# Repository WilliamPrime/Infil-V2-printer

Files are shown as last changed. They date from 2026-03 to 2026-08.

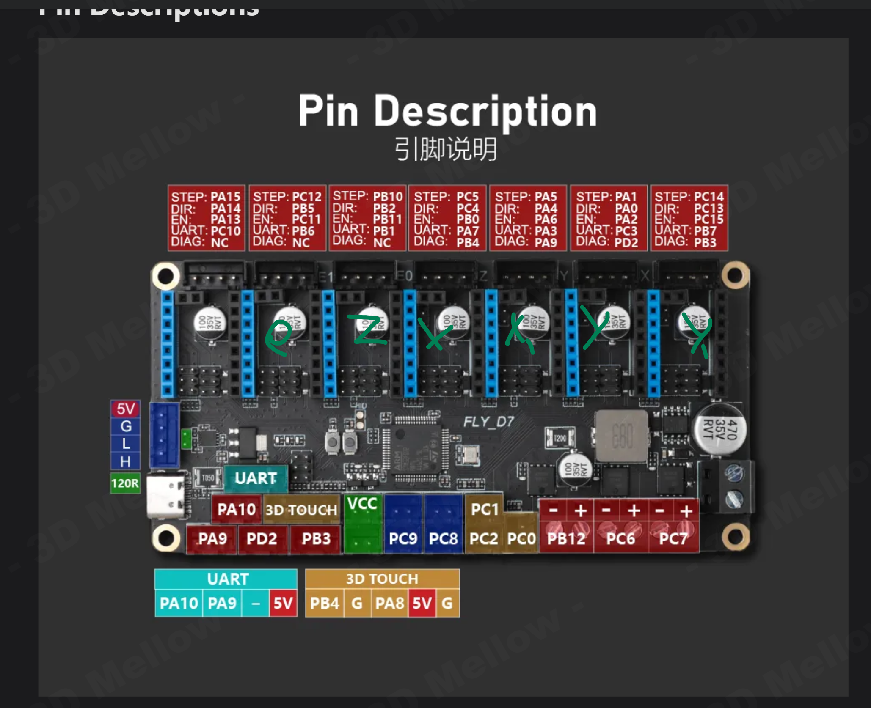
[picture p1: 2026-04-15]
Klipper/Screenshot 2026-04-15 025206.png

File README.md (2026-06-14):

# Breaky Belt

## What is Breaky Belt? 
Breaky belt is a belt printer that prints at an angle, in theory allowing infinetly long prints.

Some of the printers that inspired me to make this are:
- [Baby Belt](https://github.com/RobMink/BabyBeltPro)
- [Annex K3](https://github.com/Annex-Engineering/Gasherbrum-K3)

_DSC5262
_DSC5261
_DSC5266
_DSC5264

## why is it called the Breaky Belt?
Originally it was going to be called the Belty Boi, however, when modeling it in fusion i kept encountering issues, so it got renamed to the breaky belt.
Dont worry though, hopefully it shouldnt break on you!

An alterative name i was considering was BRRRTT, pronounced Bert, it was supposed to mimic the sound the printer makes while printing quickly.

# WARNING BEFORE YOU CONSIDER BUILDING ONE

ALL OF THE FILES IN THE REPO HAVENT BEEN TESTED YET

there are currently some issues ive encountered
1. There is a clearance issue with a couple of gantry parts removing ~10mm of x travel
2. The files have only been tested with MGN9H instead of the intended MGN9C, I accidentally ordered the wrong rails and didnt have time to order new ones
3. Electronics are currently free to roam arround whatever surface the printer is on, its not the best
4. Currently the dual SKR mini config isnt the original inteded cofig, its currently operating at 1.77A @ 24V per motor, as opposed to the 2.5A @ 48V per motor its capable of, this is due to me not being able to figure out the firmware for the board I chose, if you choose something like a btt octopus or a mellow fly super , you shouldnt run into this issue. Reguardless of how you fix it, im not exactly sure of the max capabilities of the printer at the moment, 1300mm/s @ 37K Accel was comfortable acchived without motor tuning or experimentation into rubber band systems to counter the weight of toolhead

# building it
On the topic of it breaking on you (which hopefully it shouldnt do).
When building it, I would suggest you build the bed assembly first.And assemble it as shown in the following animation

https://github.com/user-attachments/assets/72ef6f26-8bf3-4d65-aa56-422cc91b3fcc

When building it you will find the CAD for the extruder is not included
the mounting holes for the extruder support anything with the same mounting as the sherpa mini
for my build im using the [ProtoXtruder 2.0 by Nhchiu](https://github.com/nhchiu/3DPrinter-Designs/tree/main/ProtoXtruder_2.0)

# Parts/BOM

[_Here_](https://github.com/WilliamPrime/Infil-V2-printer/blob/main/BOM.csv) is the BOM

If you allready have some of the parts, [_this_](https://github.com/WilliamPrime/Infil-V2-printer/blob/main/Interactive%20BOM.xlsx) version of the bom lets you remove parts and tick them off

In terms of filament, i recomend using ABS, you will need
~1300g of primary colour
~600g of secondary colour

£

# bonus photo with Orpheus for scale
_DSC5265

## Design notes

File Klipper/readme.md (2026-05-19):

# THESE CONFIGS WORK WITH A PAIR OF SKR MINI E3 V3s 

# MODIFICATIONS ARE NEEDED TO GET THE MELLOW D7 and TMC5160s WORKING TO ENABLE 48V SUPPORT

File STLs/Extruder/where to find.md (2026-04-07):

Due to the liscence of the extruder im not including it in this repo.

My choice was the ProtoXtruder which can be found [here ](https://github.com/nhchiu/3DPrinter-Designs/tree/main/ProtoXtruder_2.0).
Another great choice for a compatible extruder is the [sherpa mini](https://github.com/Annex-Engineering/Sherpa_Mini-Extruder).

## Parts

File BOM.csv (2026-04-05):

 |  | pack size (where aplicable) | Cost | Quant | Total for item | Link | Notes
MOTION
Reinforced Gt2 belt 2M |  |  | 11.58 | 1 | 11.58 | https://www.aliexpress.com/item/1005010353468208.html | printer requires exactly 2.1meters of belt, make sure to buy a little bit more
Toothed 20t idler |  | 4pack | 16.14 | 0 | 0.00 | https://www.aliexpress.com/item/1005002630474461.html
625 bearings |  | 1pk | 0.1186 | 16 | 1.90 | https://jlcmc.com/product/b/C15/BR8364/deep-groove-ball-bearing-double-side-with-dust-cover
5mm couplers |  | 1pk | 1.56 | 4 | 6.24 | https://www.aliexpress.com/item/1005008857891214.html | 5x5 | cheaper than jlc
5mm dia 11mm shaft |  |  | 0.6632 | 4 | 2.66 | https://jlcmc.com/product/s/B08/BACA/linear-shaft-solid-straight-g6-tolerance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
5mm dia 50mm shaft |  |  | 0.75 | 4 | 3.00 | https://jlcmc.com/product/s/B08/BACA/linear-shaft-solid-straight-g6-tolerance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
5mm dia 142mm shaft |  |  | 1.1663 | 2 | 2.34 | https://jlcmc.com/product/s/B08/BACA/linear-shaft-solid-straight-g6-tolerance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
Z1 mgn9c 314mm |  |  | 10.951 | 1 | 10.96 | https://jlcmc.com/product/s/B03/E-BMN/economical-linear-guide-mini-standard-type-7-9-12-15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
Z1 mgn9c 160mm |  |  | 7.3636 | 2 | 14.73 | https://jlcmc.com/product/s/B03/E-BMN/economical-linear-guide-mini-standard-type-7-9-12-15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
Z1 mgn9c 224mm |  |  | 8.8442 | 3 | 26.54 | https://jlcmc.com/product/s/B03/E-BMN/economical-linear-guide-mini-standard-type-7-9-12-15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
LDO2504AH |  | Inc shipping 4pk | 107.87 | 1 | 107.87 | https://www.onetwo3d.co.uk/product/ldo-42sth48-2504ahs35r-stepper-motor/ | CAD uses 30mm shaft motors, these are 35mm shaft motors , spacers required
FRAME
2020 , 180mm |  |  | 0.4712 | 2 | 0.95 | https://jlcmc.com/product/s/T01/TXCJ/extruded-aluminum-t-slot-20-series(eu)?k=TXCJ-H7-2020D-L180
2020 , 280mm |  |  | 0.7272 | 2 | 1.46 | https://jlcmc.com/product/s/T01/TXCJ/extruded-aluminum-t-slot-20-series(eu)?k=TXCJ-H7-2020D-L280
2020 , 380mm |  |  | 0.9814 | 2 | 1.97 | https://jlcmc.com/product/s/T01/TXCJ/extruded-aluminum-t-slot-20-series(eu)?k=TXCJ-H7-2020D-L380
2020 , 320mm |  |  | 0.8285 | 4 | 3.32 | https://jlcmc.com/product/s/T01/TXCJ/extruded-aluminum-t-slot-20-series(eu)?k=TXCJ-H7-2020D-L320
FASTENERS
m5, 7.5mm od heatset |  | 10pk | 2.39 | 1 | 2.39 | https://www.aliexpress.com/item/1005008897571758.html
m3, m3x5x4.2 |  | 250pk | 7.86 | 1 | 7.86 | https://www.aliexpress.com/item/1005006494200941.html | you could order the exact ammount you need, but if you need to reprint a part and need more heatsets, that could become bad
M5x30 | SHCS |  | 0.0255 | 12 | 0.31
M5x20 | SHCS |  | 0.0167 | 14 | 0.24
M5x12 | SHCS |  | 0.0159 | 60 | 0.96
M5 t slot nut |  |  | 0.0099 | 54 | 0.54 | https://jlcmc.com/product/s/T02/TPAA/m3-m4-m5-t-nut-20-series-aluminum-profile-fasteners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
M4x20 | SHCS |  | 0.156 | 14 | 2.19 | https://jlcmc.com/product/s/E02/EDLA/hex-socket-screw-full-partial-thread-standard-type-(din-912-gb-t-70.1)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
M4x10 | SHCS |  | 0.142 | 5 | 0.71 | https://jlcmc.com/product/s/E02/EDLA/hex-socket-screw-full-partial-thread-standard-type-(din-912-gb-t-70.1)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
M4 t slot nut |  |  | 0.0082 | 20 | 0.17 | https://jlcmc.com/product/s/T02/TPAA/m3-m4-m5-t-nut-20-series-aluminum-profile-fasteners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
M3x40 | SHCS |  | 0.0269 | 11 | 0.30 | https://jlcmc.com/product/s/E02/EDLA/hex-socket-screw-full-partial-thread-standard-type-(din-912-gb-t-70.1)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
M3x35 | SHCS |  | 0.0273 | 5 | 0.14 | https://jlcmc.com/product/s/E02/EDLA/hex-socket-screw-full-partial-thread-standard-type-(din-912-gb-t-70.1)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
M3x30 | SHCS |  | 0.0222 | 8 | 0.18 | https://jlcmc.com/product/s/E02/EDLA/hex-socket-screw-full-partial-thread-standard-type-(din-912-gb-t-70.1)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
M3x25 | SHCS |  | 0.0178 | 7 | 0.13 | https://jlcmc.com/product/s/E02/EDLA/hex-socket-screw-full-partial-thread-standard-type-(din-912-gb-t-70.1)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
M3x22 | SHCS |  | 0.0169 | 8 | 0.14 | https://jlcmc.com/product/s/E02/EDLA/hex-socket-screw-full-partial-thread-standard-type-(din-912-gb-t-70.1)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
M3x20 | SHCS |  | 0.0143 | 3 | 0.05 | https://jlcmc.com/product/s/E02/EDLA/hex-socket-screw-full-partial-thread-standard-type-(din-912-gb-t-70.1)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
M3x16 | SHCS |  | 0.0142 | 23 | 0.33 | https://jlcmc.com/product/s/E02/EDLA/hex-socket-screw-full-partial-thread-standard-type-(din-912-gb-t-70.1)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
M3x12 | SHCS |  | 0.128 | 70 | 8.96 | https://jlcmc.com/product/s/E02/EDLA/hex-socket-screw-full-partial-thread-standard-type-(din-912-gb-t-70.1)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
M3x8 | SHCS |  | 0.0113 | 57 | 0.65 | https://jlcmc.com/product/s/E02/EDLA/hex-socket-screw-full-partial-thread-standard-type-(din-912-gb-t-70.1)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
M3x6 | SHCS |  | 0.0127 | 52 | 0.67 | https://jlcmc.com/product/s/E02/EDLA/hex-socket-screw-full-partial-thread-standard-type-(din-912-gb-t-70.1)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
M3 t slot nut |  |  | 0.0136 | 70 | 0.96
ELECTRONICS
custom v0.1 bed heater |  |  | 5.25 | 1 | 5.25 | JLC flexheater service
IEC power inlet |  |  | 2.05 | 1 | 2.05 | https://www.aliexpress.com/item/1005006990146296.html
external mosfet board to support the bed |  |  | 2.51 | 1 | 2.51 | https://www.aliexpress.com/item/1005006614952857.html
external mosfet board to support the bed |  |  | 2.51 | 1 | 2.51 | https://www.aliexpress.com/item/1005006614952857.html
Ptfe wire red |  |  | 5.69 | 1 | 5.69 | https://www.aliexpress.com/item/1005004874514644.html
Ptfe wire blk |  |  | 5.7 | 1 | 5.70 | https://www.aliexpress.com/item/1005004874514644.html
old desktop fans |  |  | 0 |  |  | hunt
meanwell lrs350-24 |  |  | 42.73 | 1 | 42.73 | https://www.aliexpress.com/item/1005004796910794.html
meanwell lrs350-48 |  |  | 44.2 | 1 | 44.20 | https://www.aliexpress.com/item/1005004796910794.html
mellow D7 |  |  | 24.03 | 1 | 24.03 | https://www.aliexpress.com/item/1005006422323624.html | it’s a much cheaper alternative to the BTT octopus or mellow super
TMC2209 | 2pk |  | 7.39 | 1 | 7.39 | https://www.aliexpress.com/item/33028050145.html
TMC5160 | 1pk |  | 21.72 | 4 | 86.88 | https://www.aliexpress.com/item/1005004229433552.html
Toolhead
peopoly lancer long |  |  | 64.99 | 1 | 64.99 | https://peopoly.net/products/magneto-x-lancer-melt-zone?variant=49972216103194 | 120w heater on it, 15 bucks of the prices is shipping
HGX 2.0 gears + hardware |  |  | 13.85 | 1 | 13.85 | https://www.aliexpress.com/item/1005007316630515.html | comes with other hardware needed
4015 fan |  |  | 2.37 | 1 | 2.37 | https://www.aliexpress.com/item/1005004832141450.html | for low speed PLA
2510 fan |  |  | 1.62 | 1 | 1.62 | https://www.aliexpress.com/item/1005003595630530.html | fan
LDO 36STH20-1004AHG |  |  | 24.11 | 1 | 24.11 | https://www.aliexpress.com/item/1005002899860754.html | Allready own, using from infil v1
OTHER
voron 0 bed |  |  | 13.73 | 1 | 13.73 | https://www.aliexpress.com/item/1005007347759654.html
bed springs |  |  | 1.09 | 1 | 1.09 | https://www.aliexpress.com/item/33000218395.html
gt2 6mm closed loop belt for belt |  |  | 1.94 | 1 | 0.00 | https://www.aliexpress.com/item/1005004019523225.html | 2gt 306 | I allready own this
motor heat sync |  |  | 3.03 | 1 | 3.03 | https://www.aliexpress.com/item/4000723868050.html
SHIPPING
If using JLC the (shipping + taxes + customs) are here, this assumes you used JLC every time I used it |  |  | 90.94 | 1 | 90.94
 |  |  |  |  | Total cost
 |  |  |  |  | 668.07

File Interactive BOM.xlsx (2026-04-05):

 |  | Total cost
 |  | 577.13
Owned? |  |  | pack size (where aplicable) | Cost | Quant | Total From scratch | Total with my parts | Link | Notes
 | MOTION
FALSE | Reinforced Gt2 belt 2M |  |  | 11.58 | 1 | 11.58 | 11.58 | https://www.aliexpress.com/item/1005010353468208.html | printer requires exactly 2.1meters of belt, make sure to buy a little bit more
FALSE | Toothed 20t idler |  | 4pack | 16.14 | 0 | 0.00 | 0 | https://www.aliexpress.com/item/1005002630474461.html
FALSE | 625 bearings |  | 1pk | 0.1186 | 16 | 1.90 | 1.9 | https://jlcmc.com/product/b/C15/BR8364/deep-groove-ball-bearing-double-side-with-dust-cover
FALSE | 5mm couplers |  | 1pk | 1.56 | 4 | 6.24 | 6.24 | https://www.aliexpress.com/item/1005008857891214.html | 5x5 | cheaper than jlc
FALSE | 5mm dia 11mm shaft |  |  | 0.6632 | 4 | 2.66 | 2.66 | https://jlcmc.com/product/s/B08/BACA/linear-shaft-solid-straight-g6-tolerance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
FALSE | 5mm dia 50mm shaft |  |  | 0.75 | 4 | 3.00 | 3 | https://jlcmc.com/product/s/B08/BACA/linear-shaft-solid-straight-g6-tolerance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
FALSE | 5mm dia 142mm shaft |  |  | 1.1663 | 2 | 2.34 | 2.34 | https://jlcmc.com/product/s/B08/BACA/linear-shaft-solid-straight-g6-tolerance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
FALSE | Z1 mgn9c 314mm |  |  | 10.951 | 1 | 10.96 | 10.96 | https://jlcmc.com/product/s/B03/E-BMN/economical-linear-guide-mini-standard-type-7-9-12-15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
FALSE | Z1 mgn9c 160mm |  |  | 7.3636 | 2 | 14.73 | 14.73 | https://jlcmc.com/product/s/B03/E-BMN/economical-linear-guide-mini-standard-type-7-9-12-15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
FALSE | Z1 mgn9c 224mm |  |  | 8.8442 | 3 | 26.54 | 26.54 | https://jlcmc.com/product/s/B03/E-BMN/economical-linear-guide-mini-standard-type-7-9-12-15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
FALSE | LDO2504AH |  | Inc shipping 4pk | 107.87 | 1 | 107.87 | 107.87 | https://www.onetwo3d.co.uk/product/ldo-42sth48-2504ahs35r-stepper-motor/ | CAD uses 30mm shaft motors, these are 35mm shaft motors , spacers required
 | FRAME
FALSE | 2020 , 180mm |  |  | 0.4712 | 2 | 0.95 | 0.95 | https://jlcmc.com/product/s/T01/TXCJ/extruded-aluminum-t-slot-20-series(eu)?k=TXCJ-H7-2020D-L180
FALSE | 2020 , 280mm |  |  | 0.7272 | 2 | 1.46 | 1.46 | https://jlcmc.com/product/s/T01/TXCJ/extruded-aluminum-t-slot-20-series(eu)?k=TXCJ-H7-2020D-L280
FALSE | 2020 , 380mm |  |  | 0.9814 | 2 | 1.97 | 1.97 | https://jlcmc.com/product/s/T01/TXCJ/extruded-aluminum-t-slot-20-series(eu)?k=TXCJ-H7-2020D-L380
FALSE | 2020 , 320mm |  |  | 0.8285 | 4 | 3.32 | 3.32 | https://jlcmc.com/product/s/T01/TXCJ/extruded-aluminum-t-slot-20-series(eu)?k=TXCJ-H7-2020D-L320
 | FASTENERS
FALSE | m5, 7.5mm od heatset |  | 10pk | 2.39 | 1 | 2.39 | 2.39 | https://www.aliexpress.com/item/1005008897571758.html
FALSE | m3, m3x5x4.2 |  | 250pk | 7.86 | 1 | 7.86 | 7.86 | https://www.aliexpress.com/item/1005006494200941.html | you could order the exact ammount you need, but if you need to reprint a part and need more heatsets, that could become bad
FALSE | M5x30 | SHCS |  | 0.0255 | 12 | 0.31 | 0.31
FALSE | M5x20 | SHCS |  | 0.0167 | 14 | 0.24 | 0.24
FALSE | M5x12 | SHCS |  | 0.0159 | 60 | 0.96 | 0.96
FALSE | M5 t slot nut |  |  | 0.0099 | 54 | 0.54 | 0.54 | https://jlcmc.com/product/s/T02/TPAA/m3-m4-m5-t-nut-20-series-aluminum-profile-fasteners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
FALSE | M4x20 | SHCS |  | 0.156 | 14 | 2.19 | 2.19 | https://jlcmc.com/product/s/E02/EDLA/hex-socket-screw-full-partial-thread-standard-type-(din-912-gb-t-70.1)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
FALSE | M4x10 | SHCS |  | 0.142 | 5 | 0.71 | 0.71 | https://jlcmc.com/product/s/E02/EDLA/hex-socket-screw-full-partial-thread-standard-type-(din-912-gb-t-70.1)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
FALSE | M4 t slot nut |  |  | 0.0082 | 20 | 0.17 | 0.17 | https://jlcmc.com/product/s/T02/TPAA/m3-m4-m5-t-nut-20-series-aluminum-profile-fasteners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
FALSE | M3x40 | SHCS |  | 0.0269 | 11 | 0.30 | 0.3 | https://jlcmc.com/product/s/E02/EDLA/hex-socket-screw-full-partial-thread-standard-type-(din-912-gb-t-70.1)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
FALSE | M3x35 | SHCS |  | 0.0273 | 5 | 0.14 | 0.14 | https://jlcmc.com/product/s/E02/EDLA/hex-socket-screw-full-partial-thread-standard-type-(din-912-gb-t-70.1)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
FALSE | M3x30 | SHCS |  | 0.0222 | 8 | 0.18 | 0.18 | https://jlcmc.com/product/s/E02/EDLA/hex-socket-screw-full-partial-thread-standard-type-(din-912-gb-t-70.1)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
FALSE | M3x25 | SHCS |  | 0.0178 | 7 | 0.13 | 0.13 | https://jlcmc.com/product/s/E02/EDLA/hex-socket-screw-full-partial-thread-standard-type-(din-912-gb-t-70.1)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
FALSE | M3x22 | SHCS |  | 0.0169 | 8 | 0.14 | 0.14 | https://jlcmc.com/product/s/E02/EDLA/hex-socket-screw-full-partial-thread-standard-type-(din-912-gb-t-70.1)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
FALSE | M3x20 | SHCS |  | 0.0143 | 3 | 0.05 | 0.05 | https://jlcmc.com/product/s/E02/EDLA/hex-socket-screw-full-partial-thread-standard-type-(din-912-gb-t-70.1)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
FALSE | M3x16 | SHCS |  | 0.0142 | 23 | 0.33 | 0.33 | https://jlcmc.com/product/s/E02/EDLA/hex-socket-screw-full-partial-thread-standard-type-(din-912-gb-t-70.1)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
FALSE | M3x12 | SHCS |  | 0.128 | 70 | 8.96 | 8.96 | https://jlcmc.com/product/s/E02/EDLA/hex-socket-screw-full-partial-thread-standard-type-(din-912-gb-t-70.1)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
FALSE | M3x8 | SHCS |  | 0.0113 | 57 | 0.65 | 0.65 | https://jlcmc.com/product/s/E02/EDLA/hex-socket-screw-full-partial-thread-standard-type-(din-912-gb-t-70.1)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
FALSE | M3x6 | SHCS |  | 0.0127 | 52 | 0.67 | 0.67 | https://jlcmc.com/product/s/E02/EDLA/hex-socket-screw-full-partial-thread-standard-type-(din-912-gb-t-70.1)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
FALSE | M3 t slot nut |  |  | 0.0136 | 70 | 0.96 | 0.96
 |  |  |  |  |  |  | 0
 | ELECTRONICS
FALSE | custom v0.1 bed heater |  |  | 5.25 | 1 | 5.25 | 5.25 | JLC flexheater service
FALSE | IEC power inlet |  |  | 2.05 | 1 | 2.05 | 2.05 | https://www.aliexpress.com/item/1005006990146296.html
FALSE | external mosfet board to support the bed |  |  | 2.51 | 1 | 2.51 | 2.51 | https://www.aliexpress.com/item/1005006614952857.html
FALSE | external mosfet board to support the bed |  |  | 2.51 | 1 | 2.51 | 2.51 | https://www.aliexpress.com/item/1005006614952857.html
FALSE | Ptfe wire red |  |  | 5.69 | 1 | 5.69 | 5.69 | https://www.aliexpress.com/item/1005004874514644.html
FALSE | Ptfe wire blk |  |  | 5.7 | 1 | 5.70 | 5.7 | https://www.aliexpress.com/item/1005004874514644.html
FALSE | old desktop fans |  |  | 0 |  |  | 0 | hunt
FALSE | meanwell lrs350-24 |  |  | 42.73 | 1 | 42.73 | 42.73 | https://www.aliexpress.com/item/1005004796910794.html
FALSE | meanwell lrs350-48 |  |  | 44.2 | 1 | 44.20 | 44.2 | https://www.aliexpress.com/item/1005004796910794.html
FALSE | mellow D7 |  |  | 24.03 | 1 | 24.03 | 24.03 | https://www.aliexpress.com/item/1005006422323624.html | it’s a much cheaper alternative to the BTT octopus or mellow super
FALSE | TMC2209 | 2pk |  | 7.39 | 1 | 7.39 | 7.39 | https://www.aliexpress.com/item/33028050145.html
FALSE | TMC5160 | 1pk |  | 21.72 | 4 | 86.88 | 86.88 | https://www.aliexpress.com/item/1005004229433552.html
 | Toolhead
FALSE | peopoly lancer long |  |  | 64.99 | 1 | 64.99 | 64.99 | https://peopoly.net/products/magneto-x-lancer-melt-zone?variant=49972216103194 | 120w heater on it, 15 bucks of the prices is shipping
FALSE | HGX 2.0 gears + hardware |  |  | 13.85 | 1 | 13.85 | 13.85 | https://www.aliexpress.com/item/1005007316630515.html | comes with other hardware needed
FALSE | 4015 fan |  |  | 2.37 | 1 | 2.37 | 2.37 | https://www.aliexpress.com/item/1005004832141450.html | for low speed PLA
FALSE | 2510 fan |  |  | 1.62 | 1 | 1.62 | 1.62 | https://www.aliexpress.com/item/1005003595630530.html | fan
FALSE | LDO 36STH20-1004AHG |  |  | 24.11 | 1 | 24.11 | 24.11 | https://www.aliexpress.com/item/1005002899860754.html | Allready own, using from infil v1
 | OTHER
FALSE | voron 0 bed |  |  | 13.73 | 1 | 13.73 | 13.73 | https://www.aliexpress.com/item/1005007347759654.html
FALSE | bed springs |  |  | 1.09 | 1 | 1.09 | 1.09 | https://www.aliexpress.com/item/33000218395.html
FALSE | gt2 6mm closed loop belt for belt |  |  | 1.94 | 1 | 0.00 | 0 | https://www.aliexpress.com/item/1005004019523225.html | 2gt 306 | I allready own this
FALSE | motor heat sync |  |  | 3.03 | 1 | 3.03 | 3.03 | https://www.aliexpress.com/item/4000723868050.html

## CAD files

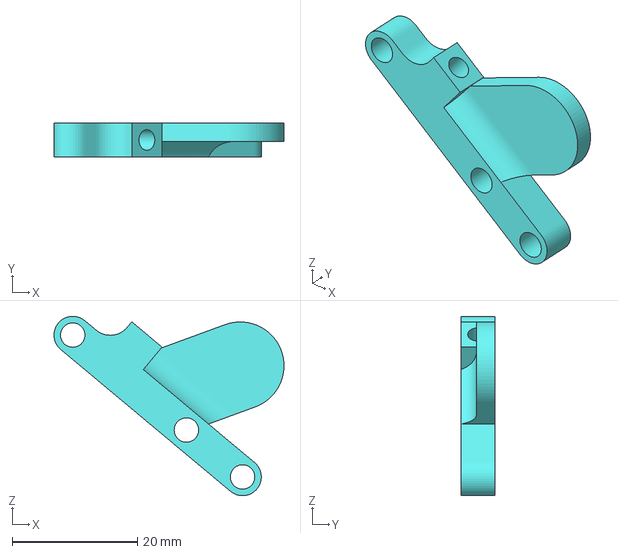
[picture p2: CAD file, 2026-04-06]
STLs/Toolhead/Accent/main fan mounting.3mf
36.7 x 5.50 x 28.7 mm

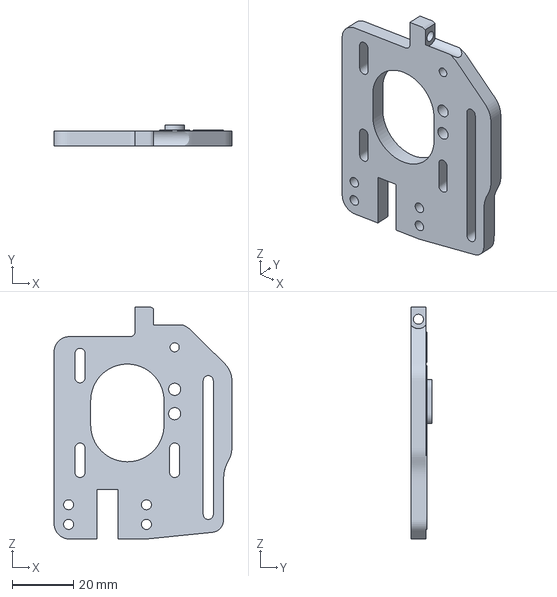
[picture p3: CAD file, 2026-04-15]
STLs/FIXES THAT NEED TO BE SORTED/new main plate.3mf
58.2 x 7.00 x 76.0 mm

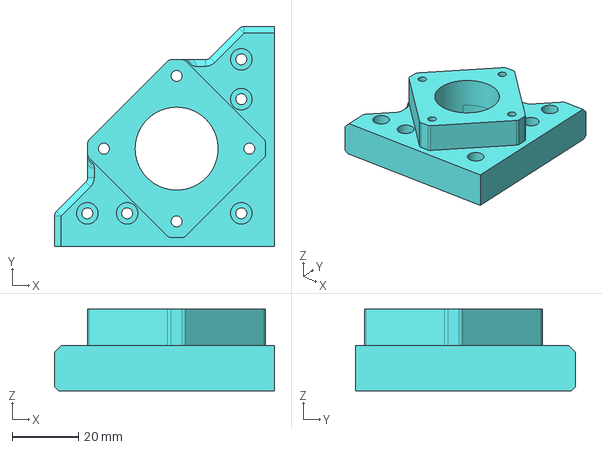
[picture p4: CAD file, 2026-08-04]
CAD/35mm shaft motor replacement plate/35mm shaft motor adaptor.step
66.3 x 66.3 x 24.6 mm

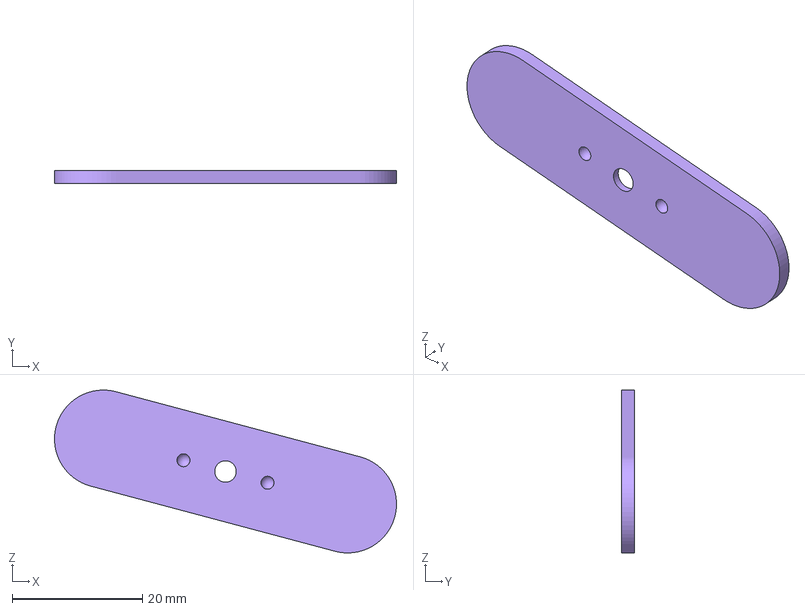
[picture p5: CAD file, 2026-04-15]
STLs/belt asembly/Accent colour/Back bearing covers -x2.3mf
52.5 x 2.00 x 25.0 mm

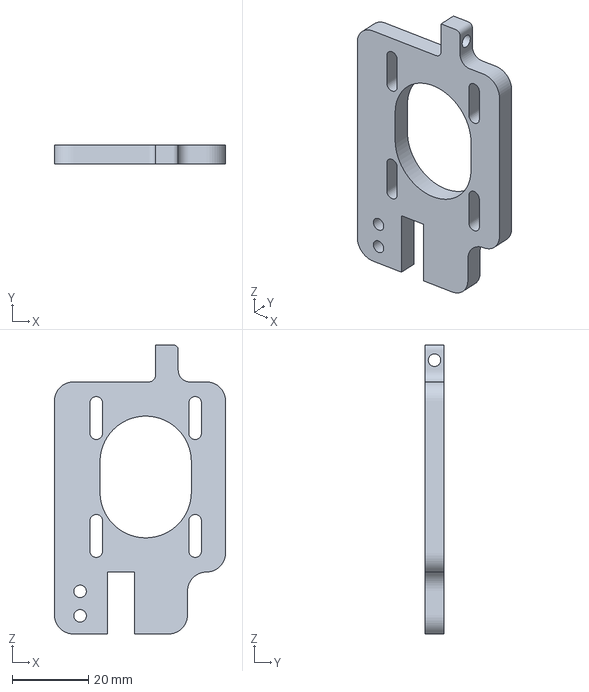
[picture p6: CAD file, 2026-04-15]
STLs/belt asembly/Primary colour/BedMotorMount nema14.3mf
45.0 x 5.00 x 76.0 mm

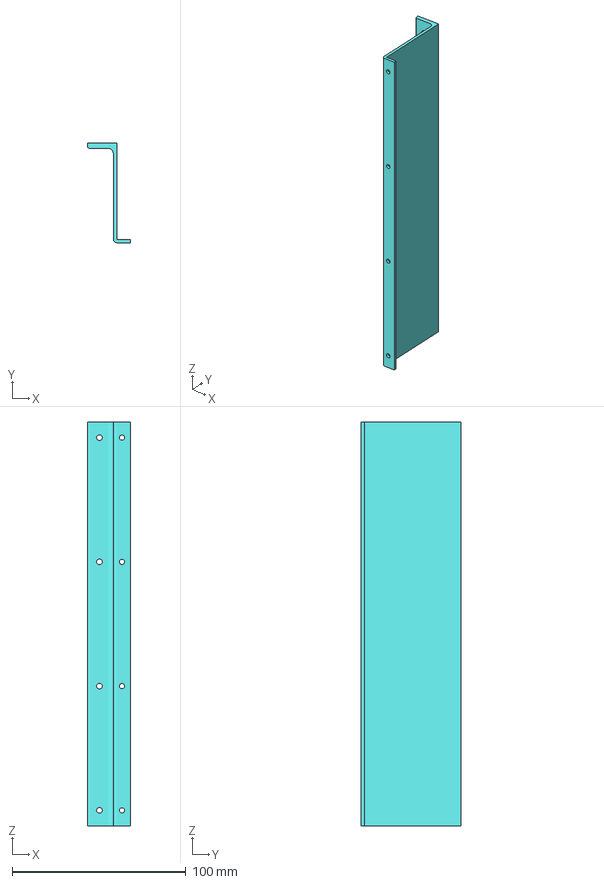
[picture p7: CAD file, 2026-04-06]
STLs/electronics/Accent/PSU cover.3mf
25.0 x 57.3 x 232.5 mm

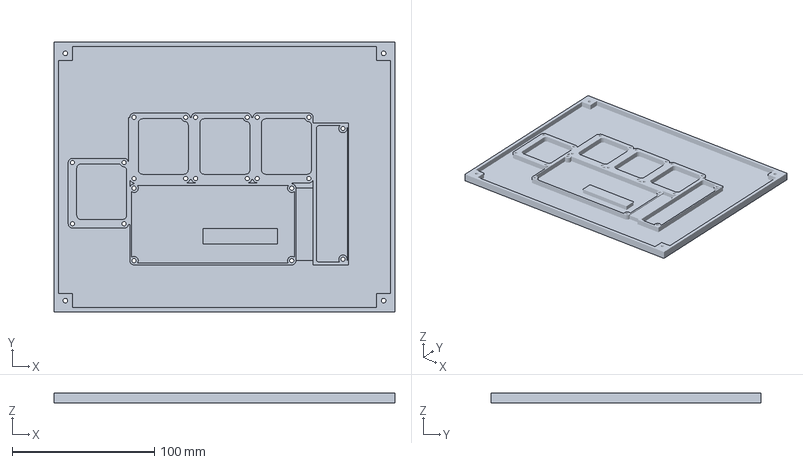
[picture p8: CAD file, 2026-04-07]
STLs/electronics/enclosure bottom.3mf
240.0 x 190.0 x 7.00 mm

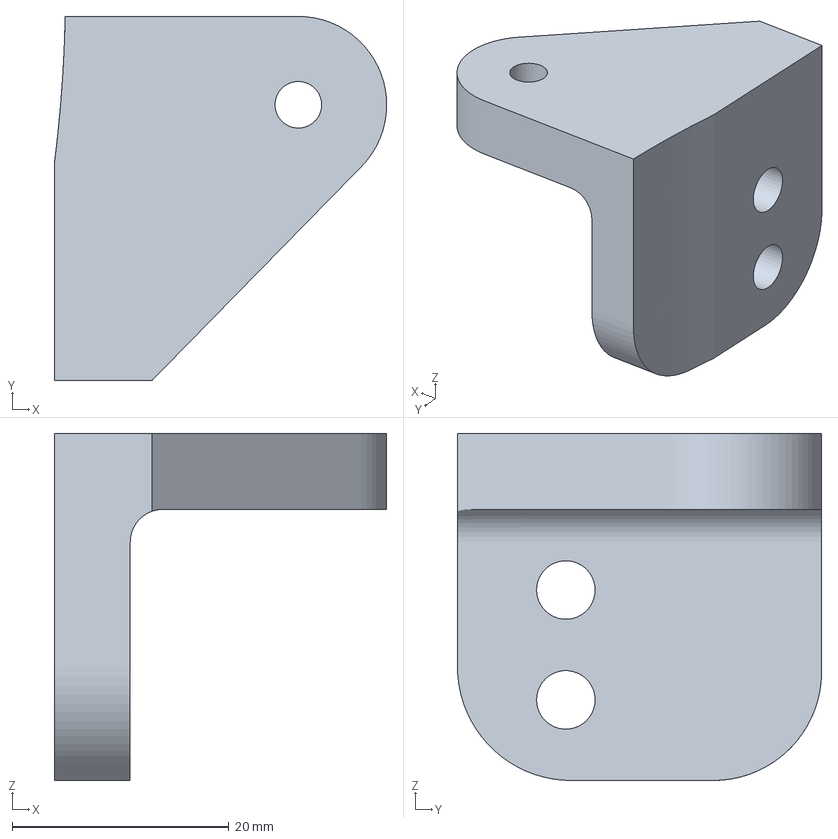
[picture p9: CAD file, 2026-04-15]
STLs/electronics/Primary/PSU mounting bracket -x2 .3mf
30.6 x 33.6 x 32.0 mm

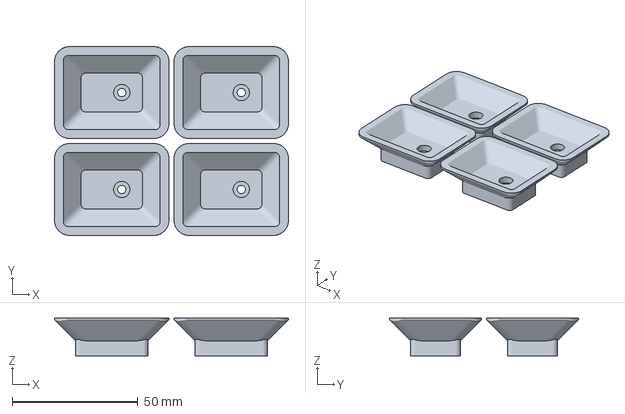
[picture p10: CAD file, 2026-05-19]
STLs/feet/feet x4 TPU.3mf
93.2 x 75.2 x 15.0 mm

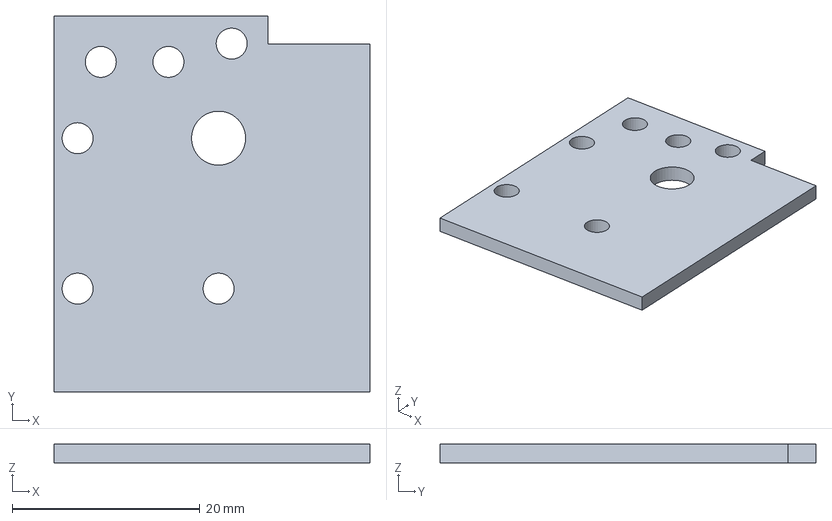
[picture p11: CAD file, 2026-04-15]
STLs/FIXES THAT NEED TO BE SORTED/MGN9h MOD/Body1.3mf
33.6 x 40.0 x 2.00 mm

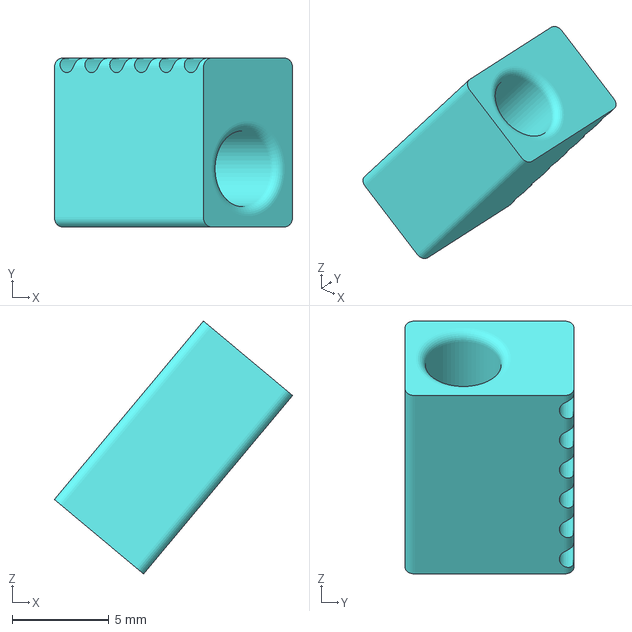
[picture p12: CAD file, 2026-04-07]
STLs/gantry/Accent/grippy block -x4 .3mf
12.3 x 8.71 x 13.1 mm

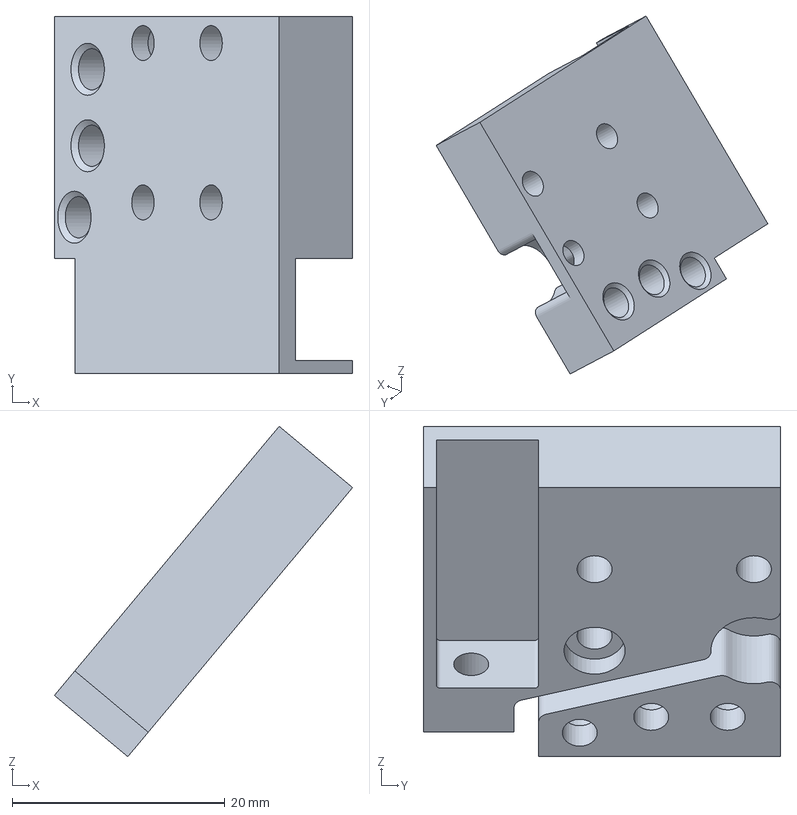
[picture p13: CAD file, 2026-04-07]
STLs/gantry/Primary/gantry mid plate right -x2 .3mf
28.1 x 33.6 x 31.1 mm

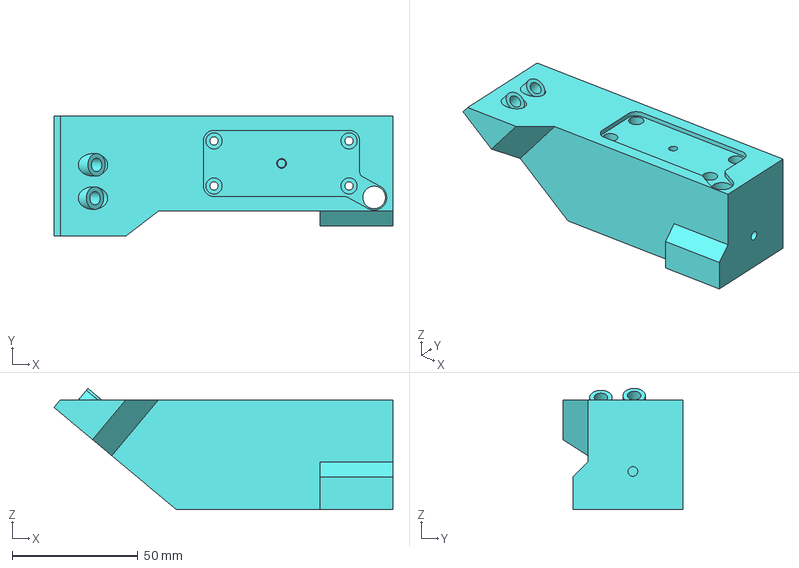
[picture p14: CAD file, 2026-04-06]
STLs/left wedge/Accent/B part.3mf
135.0 x 47.9 x 48.3 mm

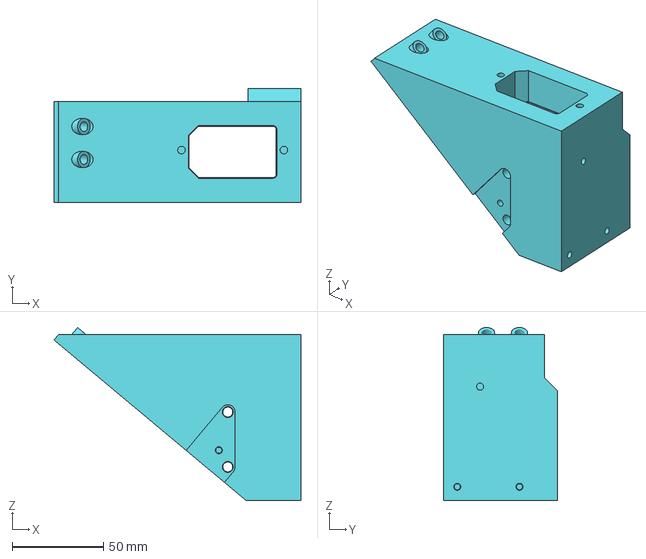
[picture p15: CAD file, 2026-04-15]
STLs/right wedge/Accent/right wedge v2.3mf
135.0 x 62.3 x 94.6 mm

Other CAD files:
STLs/FIXES THAT NEED TO BE SORTED/nema 14 new bottom plate.3mf
STLs/right wedge/Primary/black flap on wedge.3mf
STLs/Toolhead/Primary/Hotend extruder fan mount.3mf
STLs/belt asembly/Accent colour/Front bearing covers -x2.3mf
CAD/35mm shaft motor replacement plate/35mm shaft motor adaptor.3mf
CAD/35mm shaft motor replacement plate/35mm shaft motor adaptor.f3d
STLs/FIXES THAT NEED TO BE SORTED/0.6mm washer.3mf
STLs/FIXES THAT NEED TO BE SORTED/MGN9h MOD/LITTLE BLOCK.3mf
STLs/FIXES THAT NEED TO BE SORTED/MGN9h MOD/Mid plates.3mf
STLs/FIXES THAT NEED TO BE SORTED/MGN9h MOD/New chonky.3mf
STLs/FIXES THAT NEED TO BE SORTED/MGN9h MOD/SPACER BLOCK.3mf
STLs/FIXES THAT NEED TO BE SORTED/MGN9h MOD/butchered block A mirror.3mf
STLs/FIXES THAT NEED TO BE SORTED/MGN9h MOD/butchered top a.3mf
STLs/FIXES THAT NEED TO BE SORTED/MGN9h MOD/top clamp.3mf
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

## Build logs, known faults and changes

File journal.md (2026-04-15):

# 14/03/2026 Started a new BOM 1.5h

Originally i had been planning for this to be a corexy belted printer
however i had a change of mind and want to try make a croxy belted 3d printer, which will probably make things harder

if i run out of time, this might get turned into a voron 0.1 size croxy 3d printer, it really depends how things go.

Back to what i actually did

# 18/03/2026 started on a parametric frame 2h

Really just getting back into the swing of parametric CAD.
Last time i did a bunch of things in ways that fusion didnt like, so this time im trying to do things as proper as i can to stop fusion getting annoyed at me.

I then realised mounting rails on the bottom would be wayyy smarter so changed that. 


It was much quicker having allready done it once and knowing exactly what i need to use to achive the alignment. That being not the align too, but the constrain component tool.
Last time i tried to make a parametric printer i made the mistake of using the alignt tool a bunch, but i didnt realise that that didnt work well with parametric models.



im quite pleased with some of the parametric stuff i did to add the right ammount of holes to the rails.


Was there an easier way? Probably.
Did i have fun? yes!

My next task is to try figure out motor, and pulley mounting.

I will probably take inspiration from the Annex K3 for parts of the gantry


i loved this method for tensioning the belts, its so elegant and compact 


# 21/03/2026 1 hour

You probably cant tell, but when i constrained all of rails, that was done relative to the extrusions, which werent propely constrained. 
So i had to make sure everything was constrained


## well, it still wasnt properly constrained oops

i tried moving a carridge, and it was NOT happy
image (1)
so i tried to fix that, which then resulted in 


So i figured, since i should have constrained the frame, THEN the rails, and my rails and frame were both super cooked, I should remove all the constraints on the rails, and re constrain them on the bottom instead of building it all upside down.
Wow the above sentence needed more punctuation.

Anyway YIPEEEEEEEEEEEEEEEEEEEE


# 23/03/2026 gantry part 1, 1.5 hour

modelling in anything with gt2 belts is allways interesting, not difficult , it just looks messy 


i think ive gotten somewhere with belt mounting, i didnt want to make a 1 for 1 copy of the anex K3 , however this is heavily inspired by it




below is an image of the crossection of the annex k3


i still need to model in screws on mine, the key difference is that mine is in a bit of a smaller footprint , and also the anex team wrapped the belt arround an m3 bolt, i added a 0.8mm wall thickness hollow cylinder arround a bolt because i feared the bolt cutting into or damaging the belt.

# 23/03/2026 gantry part 2, 2h 

Im currently working on finalising which hardware i use and exactly how i mount the rail.

in the previous entry i was mainly focussing on making sure that everything went perfectly with the belts, this time im making sure everything goes perfectly with the rails, i REALYY need to make sure i grip these rails well.

So i plan on having 6 bolts to hold each rail in


a little detail i like was making sure that the heat set inserts on the bottom that some of those bolts screw into, are recessed so that they dont stick out and cause a misalignment against the carridge of the linear rail.


8 screws of varying length later and we have a hopefully well screwed together little assembly


a mirror and some constraints later
and we get this!



# 25/03/2026 gantry part 3, 3h

im so happy its comming together


Some of the things im aiming to achive with the cad are
- have the gantry be parametric, so i could scale it from 120x120 to 350x350 or whatever else i want
- have all the constraints modelled in properly so that you can move it arround in CAD and check for interference issues

part of the reason im actually making it parametric is because im not exactly sure what my travel distances will be, since some area will be lost depending on the size of my toolhead, so i want to be able to compensate for that



the parametric aspect of the CAD works arround 40% of the time
when it doesnt work re defining a handful of the rigid groups seems fix it which is odd to say the least

# 26/03/2026 5 hours

Trying to speed up the build a lot now

i threw together the mounting for the 625 bearings

i had been delaying this for quite a while because i wasnt sure where i was going to place the lower belt which would throw off everything.



the design wouldnt print the best in one peice , also wouldnt be very easy to use a vice to press fit the bearings

so ive split it into two parts



but i also believe alignment of these two parts is quite important , so in addition to the m4 bolts that will hold the halves together there will also be locating features 



Ive added 0.2mm of clearance between the locating geometries so hopefully they should fit okay

oh yeah

shoutout to autodesk for making custom length bolts a payed feature

i get the mild inconvenince of making my own parametric bolts, which really doesnt take long

It should be able to be copied and used for all the other once since i have "A config" and "B config" which flip which is the idler , and which is the pulley



spotting this wasnt great


however couplers like these exist

which mean i dont need to redesign anything which is amazing



Realised i need to rework this as theses are far to close

In the process of fixing the above issue i also discovered the holes for the motor attachment were slightly ofset, meaning i had to remove and readd the motor mounting holes. I am however glad that it was simply the motor mounting holes and not the motor which is aligned with a bunch of other stuff

ah this is a lot of errors


Given the ammount of errors i was getting I decided the best course of action would be to export the completed assemblies, like the ones for the motor / pulley mounting. Then go back to an earlier version of the file without the errors and import the assemblies to get a much cleaner doc,


i still need to import the rail holders again, but this looks a lot better, and takes way less time to compute when changing perameters

# AHHHH 27/03/2026 6h

lovely how in fusion its shown as 
but once you dare to look at it
it turns into this AHH
fussssiiioonnnnn 



it appears exporting as a step
and then importing fixes the issues?
im not exactly sure how that works but ok fusion

if we ignore bits of floating here and there its starting to look quite good


time to fix the floaties

Screws first


i could have just made a block, and i did
but i felt like doing something a little fun just because ive been doing CAD for 6 hours straight at this point

i know infil could have reduced the weight, but i just like hexagons

wow this is definetly comming together quickly now


sumarry of what ive done so far today
- made progress on a bunch of stuff
- broken a bunch of stuff

To elaborate what i meant when i said breaking a bunch of stuff, i managed to create circular dependancies, amongst other unpleasant things, which resulted in the file breaking or crashing any time i attempted to change the perameters of the frame.

So my solution to that was to once again export the completed assemblies as step files
and then make a new file to recombine them all into again
which fixed the issue

in the image below you can see me trying to make sketches to work out roughly where i was allowed to with my hotend without it coliding with the frame

i could then export that sketch into the file where i was building my hotend



modelling in no go zones so i can rearrange things with more awareness for how it interacts with the frame






might just be the worst looking duct ive ever made, or ever seen
but if it cools, it cools

i can prob use aux cooling if i really need

It needs to be at an angle because its a belted printer

i was also really limited on the fan placement because of the gantry
soo there is probably a far better way to do it

# 28/03/2026 5 hours

Modelling the no go zones REALLYY helped me work out how to arange things.

ive tried to design the printed parts so that they are easy to print since the last printer i designed had some rather akward and support needing parts.




hopefully its not awful to print

Anddd i think thats the hotend
hotend r1
hotend r2
hotend r3
hotend r4
hotend r5

the hotend took me a bit longer that i expected, but hopefully it should all join together well when i bring it back into the other file

 # 29/03/2025 1h

stuff is all comming together now, well, we can ingore the parts that spontaneously broke
 

 now its fixed i can check if my clearances are working out ok, if i did everything right the carridges should hit the end before anything on the hotend colides with the frame
 this one looks good
 

this one doesnt look like a pass

however


its a pass

this corner is not the best at all


then this corner is ok


overall i dont think i did a bad job

the moment of truth now is working out if i can change parameters without it breaking or crashing

it did it without crashing however it broke in some places again


an export an import later and i think its fixed

Some things i did on my hotend that i forgot to mention earlier

the first is im going to need to remove or use a hacksaw to make this tube shorter


the second is i plan on using superglue to help secure the 4020 fan
i didnt believe the two screws one above the other would sufficiently secure the fan, so i added little spur to the side which i could use superglue, or double sided tape, or PVA etc



my plan for the duct at the moment is also just tape, i believe once i have the parts i will need to iterate on that in significant ways


Here are some renders of what its like now
main r4
first render of it

# 29/03/2026 working on the bed/belt assembly, 3 hours

started working on belt assembly again











using those mesurements i can find the perimeter to be

93+93+ (( (360-153)/360) x 57 x pi) + ((153/360) x 12.8 x pi)

which evaluates to be 306mm
so my minimum belt length is 306mm , and therefore my max should be arround 318mm

back to the rollers
i could have left them as plain cylinders, however that feels rather boring



for the sillies i also decided that the spoke count, width and radii for the chamfers should be parametric



so putting all of that together we get this
bed assebmyl current state

# 3/03/2026 belt time and approaching the finish for the CAD , 8 hours

Im aiming to design some sort of mechanism between the two flats that push against each other to acomplish bed tensioning


more refinement


ive treally tried to keep these parts printable so far



im a bit scared of the shafts wiggling out of the bearings


this with a screw could be a solution, especially since it would add a splash of colour

lil render whatever

i added some little inxdexing indents to help align the blue parts


i love how it looks, however adjusting the bed screws, or the motor belt tension looks like a rather large pain


I might just have to accept that

my plan for tensioning is to have two blocks, the screw really tighly into the frame, and then push against two of the belt mounts to slide them.







its not the most elegant, or elegant at all, however it should be functional



luckily the tensioner should be able to be removed after youve finished tensioning

i think this has just proved that there is very little space to mount the bed with this method of tensioning



I think a tensiong method that pulls the belts tight instead of pushing them should be better for the printer


I think this is good now, its bigger and less compact than the previous tensioning design, however it grants me more room to try and configure the bed mounting and other things.


extending out to the other side gets us here, ive decided to leave an 8mm gap between the tensioner and the bottom peice, i think this is enough room to tension the bed belt




Putting everything together gets us to here


weirdly though more stuff has become misaligned, and i cant work out which constraint has messed it up which is annoying


# 03/04/2026 continuing to try make things work ,22 hours (days total)

turned out fixing those screw alignment issues went a LOT deeper than i thought
so im going to remove the hotbed assembly and try and do it again, hopefully a good chunk better


my strategy for restarting is export the thing that worked, and dont have much that can go wrong, then build from those

i thought the bed would be an easy thing to nab from the previous version but it turns out it had a ton of unessesary positionings that caused it to cause issues


ive fixed those issues now making it actually usable.
It doesnt look very different but it is different in the fact it doesnt break everything if you import it into another project.


"It doesnt look very different but it is different in the fact it doesnt break everything if you import it into another project."
It still breaks everything somehow.
Im not sure why fusion is remembering stuff about it, so im going to export it as a step and them import it to hopefully remove this sillyness.

Just exporting and reimporting the bed did not fix it, I believe its the belt thats causing issues for some reason.
fusion throws errors like this when i try and export the belt which definetly means ive done something weirdly with constraints.


I believe the best course of action now is to export it as a STEP file, and then import it again, and reconstruct the rigid groups and constraints only where needed in a smarter way.

interesting how after importing it the only part that wasnt preserved was the belt. I think that reinforces my hypothesis that it was that belt causing the issues

20-30min later and ive rebuilt all of the assemblies without any issues




I just realised ive made an  "interesting" choice, the drum that moves is the ones thats drive by the motor, so by moving that drum it adjusts the bed belt tension, but also the bed motor belt tension.

This just means that when tensioning the belt you need to remove the tension from the motor, and add it back after.
This could be improved by moving the tensioning mechanism to the other side.
For now i will stick to this design, however i plan on changing that in the future

I found a solution to the above issue.
The two bed rollers are the same in every single way, nothing stops me from swapping them, so its a very quick fix which i will do now

before:


after:


A subtle difference that should save a headache down the road

at some point when making a 3d printer with belts, i allways seem to run into something that requires solving a maths problem


like the above one, in that problem the perimeter of the shape is given, and you need to find the length of the tangent.

that was a surprising chunk of maths to go through 

i got it in this form
where p is the perimeter of the shape, the length of the belt, and then x is the length of the tangent


for l=308 it solves to ~63.32

now that i know the belt loop size and i can make it in CAD i can place in the motor.
my random picking of the bed orientiation seems to not be the best as one of the bed screws is going to interfere.


rotated it 180deg, fixed!


im working on getting something to hold the motor in place for the bed belt, i do need to make it look a bit better though


a small fillet goes a long way in making things look better


so does some colour


here is a render of how the bed assembly is comming along
new new belt assembly v5

## ive decided i want to see a bit of progress, so im putting together the gantry 
wow waiting for fusion to compute stuff is terrifying, im so scared it will crash.
After adjusting those ofsets fusion took 58 seconds to compute all of that, which is scaryily long for it to be unresponsive.

Ive also adjusted the positioning of the linear rails since there was some additional build that i could get by simply better positioning the rails



and a little bit more optimising later and the frame is 6mm smaller


component count is also starting to go up now its all in one file


wow it looks, like -- something,
something top heavy.
oh no

the width of the bottom part is 170mm
the width of the top part/gantry is 264mm

While attaching the gantry to the bed, i needed to add heat sets and holes into parts in the gantry, which meant i had to unlink the gantry.
It took fusion 2minutes and 24 seconds to break the link which is, a while.
Fusion manages to keep me on the edge of my chair

fusion has suddenly decided to be REALLY stupid 


I think the best option now is to just export as a .step and import, and make it one big rigid body to prevet things moving.
not the way i wanted to do it, but ive allready validated the build volume will be good in a different file.

On the upside i started on a klipper config while it tried to compute.

ive managed to get fusion to behave

currently im just trying to get an extra aluminium extrusion into the design so improve the rigidity of the printer


i did spot something questionable about my design, which is that the hotend in theory can print wayyy out away from under the bed, which i imagine probably would be great, however i do have a voron 0, so if i take the build plate from that and run two beds to extend it, it could work perfectly fine, that would also be pretty easy since the bed will just attach to the aluminium extrusion.


i did a chunk of BOM optimising, given the short time frame, JLC MC seems like a REALLY good choice for the linear rails, and because that means im allready getting stuff from there buying bearings and extrusions from there also saves a bunch of money, even if the shipping is expensive.

back to working on the frame

my strategy for joining everything together has been trying and get the holes in place with everything being 1 body, so its easier to reference features, and then use the split body tool to split things off after im done.



some work later and those extrusions are in which should make the printer a lot more rigid
comming together

Its really taking shape now

The last functional thing to design is the bed mounting, but thats mostly done at this point, there is just a little bit left mounting the bed holder to the frame.
Then its just the electronics enclosure and cleaning up this repo and gettting it shippable.

just one more

## onto the bed mounting

I realised i could make the bed mounting plate bigger, as it shouldnt interfere with the tensioning mechanism for the belt as long as the bits i add arent super thick, which is fine by me!

Before:


After:


I had to be very careful with how i positioned the mounts as to not obstruct the tensioning for the belt for the bed motor


also made a few changes such as this ridge now attaches with bolts to enable a far better print orientation.


## Electronics Bay 

My idea is to get all of the electronics on one 3d printed plate and then go about attaching that somewhere.

Like this


Given this printer will have 48v i really need to take saftey seriously, its a printer that will be at a 3d printing convention, i need to make sure its safe.

My plan to do that is to have all of the mains in a seperate chamber, and then run the 24v and 48v into another chamber above it


Ive also added PSU brackets beacuse those are probably a useful thing to have, it gets a bit tricky without them.



my strategy at first was make a big box , however i might need to fly with it, so now its a big box that can flatpack down, which sort of made me restart in how i designed it, but its fine.

Im trying to make it a nice box at least, making the bolts recessed where possible, that should also help me if/when i mount it


Im oddly satisfied with the enclosure


Now i get to count all the screw for my bom!

## I finished counting the all of the screws!
the screw counts are quite high, my strategy for the screws was to remove every component in the printer one by one, count it if its a screw, and then keep going until there is nothing left.

# THE PARTS ARE ORDERED :yay:

# 04/04/2026
mostly taking a breaking after the CAD-athon yesterday

# 05/04/2026 2 hours

Most of my effort today has been cleaning  up the repo and the BOM

I also remembered that since i changed the design of the bed to have the extra peice, i needed to make a cut and add a supporting peice.
I also took the chance to add an extra screw to support the motor from the other side.


# 06/04/2026 3 hours

today i have mostly been exporting all the parts to 3mf so they can be printed.

In doing that it lets me double check everything is ok.

i did find this conflict with one of the wedges interesecting with a PSU bracket


my solution was to split the offending bracket into two peices and integrate the mounting for the PSU into it.




i split it into two halves to:
- avoid needing really long hex bits/alan key
- make printing the parts easier

now it looks like this!



I just need to add some heat sets to join the two halves together now

i have also just finnished exporting all of the 3mf files so i can print the parts once i have filament

uploading the 3d printer source STEP file is a bit interesting due to the 300MB size
however i was able to get it under the 50MB file limmit with LZMA compression with a large dictionary size

# waiting for the parts to arrive

# STARTING THE BUILD 13/04/2026 

A significant number of my parts arrived!
I did however make the mistake of ordering mgn9h instead of mgn9c which means that i need to adjust the design a chunk to make it work

The first changes i made were to the hotend assembly



I also need to cut chunks out of other places in order to retain the full build volume 

such as cutting 3mm off the face of this


14/04/2026

- all my electronics arrived, drivers, mainboard etc
- closed loop gt2 issues

15/04/2026

(notes so i remember stuff later)
flashing klipper
mellow d7

was using 
~/klippy-env/bin/python ~/katapult/scripts/flashtool.py -d usb-katapult_stm32f072xb_MELLOW-if00
what worked was 
~/katapult/scripts/flashtool.py -f ~/klipper/out/klipper.bin -d /dev/serial/by-id/usb-katapult_stm32f072xb_MELLOW-if00

ah i think the first command would have worked had i used the full address, but mellows documentation was not the clearest. 
[this](https://klipper.discourse.group/t/unable-to-flash-klipper-after-installing-katapult/24266/4) was super helpful! 

# left to do 
- [x] put bed and gantry together
- [x] electronics bay
- [x] check build volume
- [X] final count of screws so i can finish bom
- [X] source motors
- [X] renders for readme
- [X] generate clean readme
- [x] create STLs/3MFs for the parts

# future improvements
- [ ] add support for nema 14 motors for the bed motor

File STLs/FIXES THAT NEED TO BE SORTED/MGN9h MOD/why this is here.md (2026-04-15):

When designing a printer arround mgn9c rails

build it with mgn9c rails

dont order mgn9h rails

i ordered mgn9h rails

i didnt mean to order mgn9h rails

this folder is super messy because its my pannicked effort to get the printer working with mgn9h rails

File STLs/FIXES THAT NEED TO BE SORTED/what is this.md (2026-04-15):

TLDR, i made ooopies

this is the fixes for them

if this folder is empty it means that either
- there are issues i havent found yet
- i have fixed all the issues

if there is stuff here it means that something is wrong

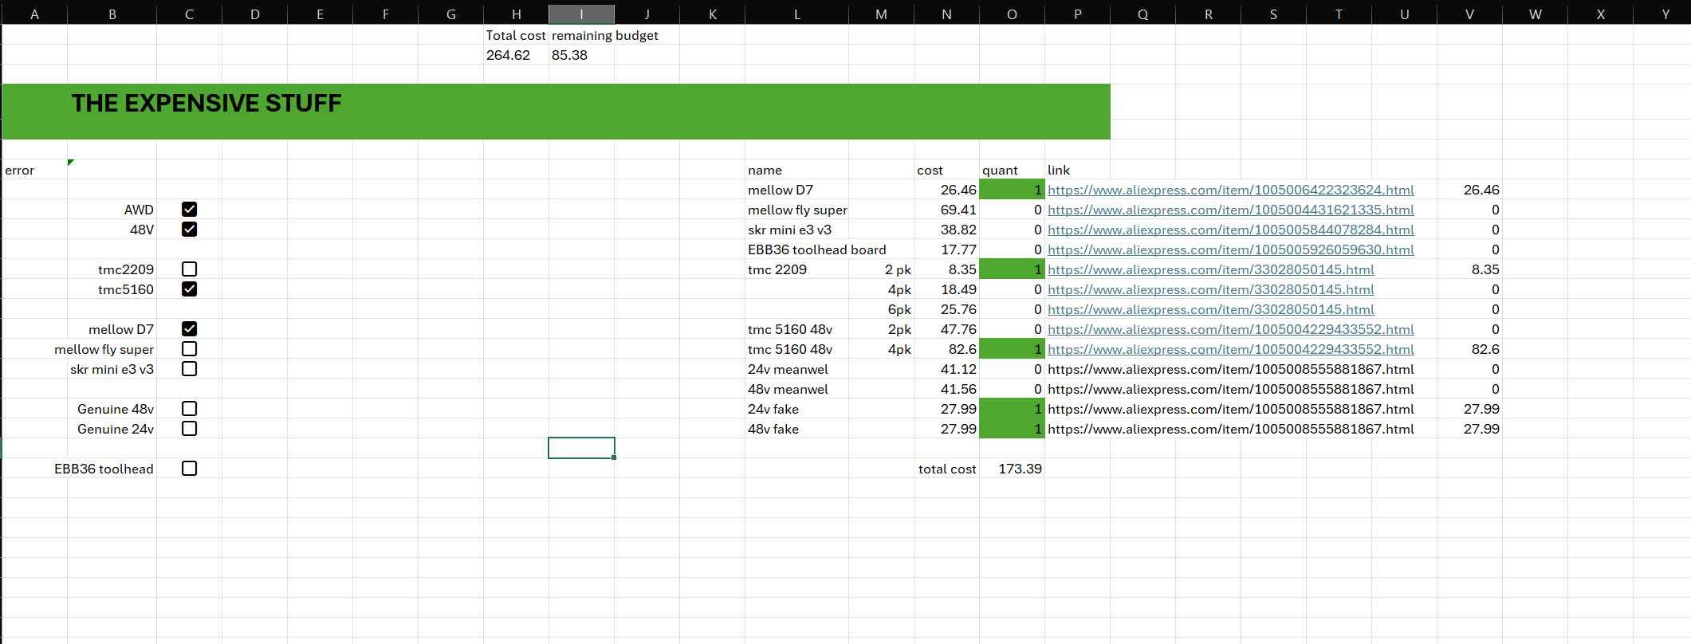
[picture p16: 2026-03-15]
imgs/journal/Screenshot 2026-03-15 130508.png

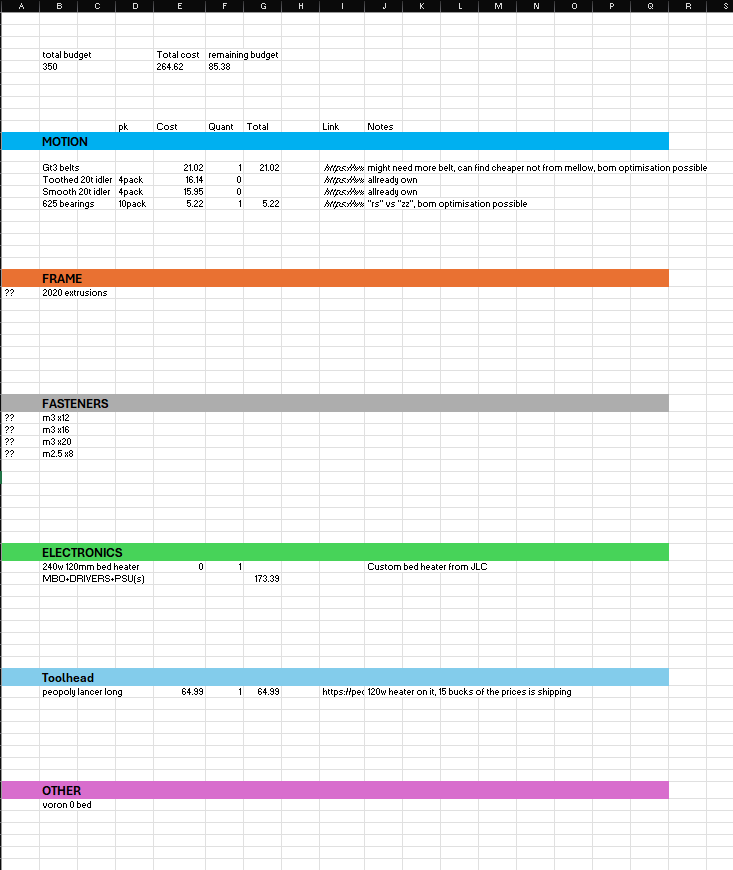
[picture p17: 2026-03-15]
imgs/journal/Screenshot 2026-03-15 130454.png

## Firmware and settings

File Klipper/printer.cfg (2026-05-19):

# =============================================================================
# Hardware: 2x BTT SKR Mini E3 V3 (TMC2209 drivers)
# Homing: Sensorless (StallGuard via TMC2209 DIAG pins)
# make sure you have a yth
#
# WIRING NOTES:
#   stepper_x  -> Board 1, port: EM  (E motor port)
#   stepper_x1 -> Board 1, port: ZM  (Z motor port)
#   stepper_y  -> Board 1, port: YM  (Y motor port)
#   stepper_y1 -> Board 1, port: XM  (X motor port)

#   stepper_e -> Board 2, port: XM  (X motor port)
#   stepper_z  -> Board 2, port: YM  (Y motor port)



[include mainsail.cfg]
[include macros.cfg]
# =============================================================================

# -----------------------------------------------------------------------------
# MCU
# Replace the serial path with your actual device path.
# Run: ls /dev/serial/by-id/ to find it.
# -----------------------------------------------------------------------------
[mcu]
serial: /dev/serial/by-id/usb-Klipper_stm32g0b1xx_4200090007504E5238363120-if00

[mcu mcu2]
serial: /dev/serial/by-id/usb-Klipper_stm32g0b1xx_200021000650414235363020-if00

[force_move]
enable_force_move: true

# -----------------------------------------------------------------------------
# PRINTER / KINEMATICS
# -----------------------------------------------------------------------------
[printer]
kinematics: cartesian

max_velocity:2000
max_accel:60000

max_z_velocity:300
max_z_accel:300

minimum_cruise_ratio: 0

# =============================================================================
# STEPPER MOTORS
# =============================================================================


# -----------------------------------------------------------------------------
[stepper_x]
step_pin: PB0
dir_pin: !PC5               # Add ! to invert if motors fight each other
enable_pin: !PB1
microsteps: 16
rotation_distance: 40
endstop_pin: tmc2209_stepper_x:virtual_endstop
position_min: 0
position_endstop: 100        # Currently limmited to 100 due to a little issue , can be fixed with a future 3d printed part swap
position_max: 100       # Currently limmited to 100 due to a little issue , can be fixed with a future 3d printed part swap
homing_speed: 40
homing_retract_dist: 0     
homing_positive_dir: true 

[tmc2209 stepper_x]
uart_pin: PC11
tx_pin: PC10
uart_address: 1            
run_current: 1.4 # for ME, cold motors 0.8A , warm motors 1.4A , COOL THE MOTOROSSSSSS PLEASEEEEE 1.77A + 
stealthchop_threshold: 0
diag_pin: ^PC2
driver_SGTHRS: 80

# -----------------------------------------------------------------------------
[stepper_x1]
step_pin: PB3
dir_pin: PB4               # Add ! to invert direction if needed: !PB4
enable_pin: !PD1
microsteps: 16
rotation_distance: 40    


[tmc2209 stepper_x1]
uart_pin: PC11
tx_pin: PC10
uart_address: 3       
run_current: 1.4     # for ME, cold motors 0.8A , warm motors 1.4A , COOL THE MOTOROSSSSSS PLEASEEEEE 1.77A + 
stealthchop_threshold: 0   

# -----------------------------------------------------------------------------
[stepper_y]
step_pin: PB13
dir_pin: !PB12              # Add ! to invert direction if needed
enable_pin: !PB14
microsteps: 16
rotation_distance: 40
endstop_pin: tmc2209_stepper_y:virtual_endstop
position_min: -1
position_endstop: -0.2     
position_max: 180         
homing_speed: 40
homing_retract_dist: 0    
homing_positive_dir: false 

[tmc2209 stepper_y]
uart_pin: PC11
tx_pin: PC10
uart_address: 2            
run_current: 1.7
stealthchop_threshold: 0
diag_pin: ^PC1
driver_SGTHRS: 80        # Tune this

# -----------------------------------------------------------------------------
[stepper_y1]
step_pin: PB10
dir_pin: PB2               # Add ! to invert if motors fight each other
enable_pin: !PB11
microsteps: 16
rotation_distance: 40

[tmc2209 stepper_y1]
uart_pin: PC11
tx_pin: PC10
uart_address: 0            
run_current: 1.4 # for ME, cold motors 0.8A , warm motors 1.4A , COOL THE MOTOROSSSSSS PLEASEEEEE 1.77A + 
stealthchop_threshold: 0
diag_pin: ^PC0

# =============================================================================

[stepper_z]
step_pin: mcu2:PB10
dir_pin: mcu2:PB2              
enable_pin: !mcu2:PB11
endstop_pin: ^mcu2:PC14        # Hahahaha, i added this so klipper stops being angry

rotation_distance:83.76
microsteps:32
full_steps_per_rotation: 200
                          
position_endstop:0                       # A Z endstop? We dont need that where we are going
position_min: -10
position_max: 10000             # YIPEEEEEEE ALLL THE Z! 
homing_speed: 10

[tmc2209 stepper_z]
uart_pin: mcu2:PC11
tx_pin: mcu2:PC10
uart_address: 0                
run_current: 0.900             # i found ths okay for the nema 14 i was using
stealthchop_threshold: 999999  # i used stealthchop, otherwise it was really loud


# =============================================================================
# EXTRUDER
# =============================================================================

[extruder]
step_pin: mcu2:PB13
dir_pin: mcu2:PB12             # Add ! to invert if needed
enable_pin: !mcu2:PB14
microsteps: 16
rotation_distance:2.816        # Calibrate for your specific extruder, i have a feeling my values are weird
nozzle_diameter: 0.400
filament_diameter: 1.750
heater_pin: PC9           
sensor_type: Generic 3950   # Change to match your thermistor
sensor_pin: PA0           
min_temp: 0
max_temp: 280
min_extrude_temp: 10
control: pid                   # Run PID_CALIBRATE HEATER=extruder TARGET=200
pid_Kp: 21.527                 
pid_Ki: 1.063
pid_Kd: 108.982

max_extrude_only_distance: 110

[tmc2209 extruder]
uart_pin: mcu2:PC11
tx_pin: mcu2:PC10
uart_address: 2               
run_current: 0.6            # depending on your E motor you might want more or less
stealthchop_threshold: 999999


# =============================================================================
# HEATED BED
# dont heat it up too much or you WILL have issues
# =============================================================================

[heater_bed]
heater_pin: PC8
sensor_type: Generic 3950
sensor_pin: PC4
control: pid
pid_Kp: 54.027
pid_Ki: 0.770
pid_Kd: 948.182
min_temp: 0
max_temp: 50 #going past 50 softens my bed adhesives a bit tooo much


# =============================================================================
# FANSSSSSSSSS
# =============================================================================

[heater_fan hotend_fan]
pin: PC6
heater_temp: 50


[fan]
pin: PC7

# the SKR mini E3 V3s get TOASTY if you run them at 1.77A , a fan is NEEDED otherwise they will shut off
[fan_generic electronics]
pin: PB15

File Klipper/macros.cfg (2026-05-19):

[homing_override]
axes: xyz
set_position_z: 0
gcode:
    G90                         ; Absolute positioning
    G28 Y
    G0 Y10 F600
    G28 X}
    G0 X40 F6000


# =============================================================================
# MACROS
# =============================================================================
 
[gcode_macro PRINT_START]
gcode:
    G28                         ; Home all axes
    G90                         ; Absolute positioning
    G92 E0                      ; Reset extruder
 
[gcode_macro PRINT_END]
gcode:
    M104 S0                     ; Turn off extruder
    M140 S0                     ; Turn off bed
    M84                         ; Disable motors


    

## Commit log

2026-03-15 Add journal entry for new BOM project
    Documented the start of a new BOM project and initial thoughts on printer design.
2026-03-20 Update journal with parametric frame progress
    Document progress on parametric frame design and adjustments made for better alignment and mounting.
2026-03-23 Add journal entry for 23/03/2026
    Added new journal entry about modelling with GT2 belts and design inspirations.
2026-03-26 Update journal with build progress and design changes
    Documented progress on the build, including design changes for the 625 bearings and the addition of locating features for alignment.
2026-03-27 Fix motor attachment holes and clean up errors
    Reworked motor attachment holes and cleaned up assembly errors by exporting completed assemblies and reverting to an earlier version.
2026-03-30 Update journal with images and perimeter calculations
    Added images and calculations for perimeter and belt length.
2026-03-30 Revise journal entry for 29/03/2026
    Updated journal entry with details on the bed/belt assembly work and added new images.
2026-04-05 Add testing notice to Klipper README
2026-04-05 adding stuff
    [BOM.csv, BOM.xlsx, Interactive BOM.xlsx]
2026-04-06 Revise README with build instructions and extruder details
    Updated the README.md with additional information about building the Breaky Belt printer and included details about the extruder.
2026-04-06 Added step files
    Also added V39 source
    [A part.3mf, B part.3mf, Back bearing covers -x2.3mf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]
2026-04-06 Update journal with 3D printer assembly details
    Documented progress on 3D printer assembly and part exporting.
2026-04-06 Update README with filament info and fixes
    Added filament recommendations and corrected minor typos.
2026-04-07 added 3MF files
    [A part.3mf, A sides -x2 .3mf, B part.3mf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]
2026-04-15 the fixing of broken stuff. maybe
    [0.6mm washer.3mf, Back bearing covers -x2.3mf, BedMotorMount nema14.3mf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]
2026-04-15 update printer.cfg
    still not tested just wokring on it while parts print
    [printer.cfg]
2026-05-19 Added klipper files
    These should have been added a lot sooner, but here they are!
    [feet x4 TPU.3mf, macros.cfg, mainsail.cfg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]
2026-05-19 Oops the klipper CFG, for real this time!
    Last time i accidentally added the mainsail.cfg instead of the klipper.cfg
    KLIPPPPPERRRRR WOOO
    [mainsail.cfg, printer.cfg]
2026-06-07 Revise README for Breaky Belt project
    Updated the README.md to improve clarity and add images.
